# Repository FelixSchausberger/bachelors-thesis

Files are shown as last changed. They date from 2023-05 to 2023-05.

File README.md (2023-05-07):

# Design and Construction of a Delta Robot to Study Inverse Kinematics

Bachelor's thesis: University of Applied Sciences Technikum Wien, 2019
This project aims at designing a delta robot to study inverse kinematics in an educational environment.

<p align="center">
  <a href="https://github.com/FelixSchausberger/bachelors_thesis">
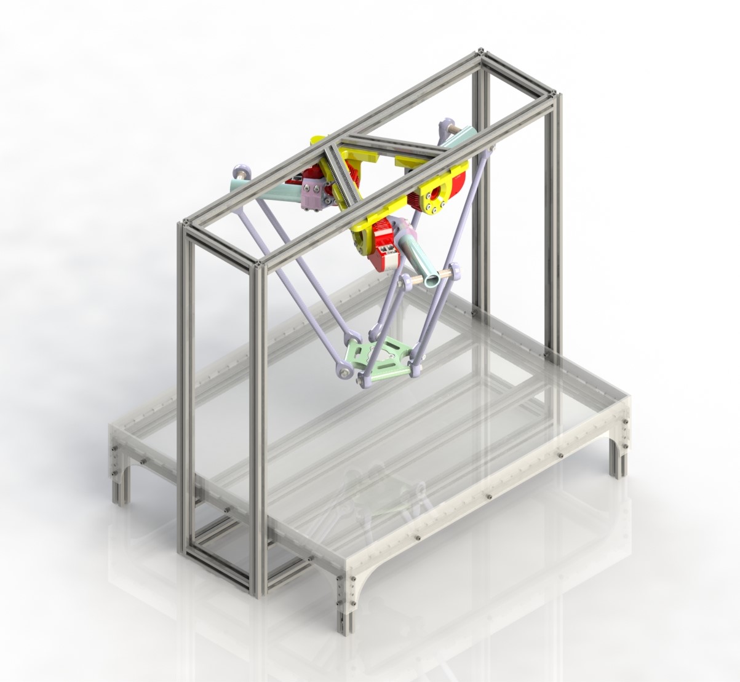
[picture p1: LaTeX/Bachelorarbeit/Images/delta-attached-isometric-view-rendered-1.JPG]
Delta Robot
    
  </a>
</p>
<br/>
<p align="center">
  <a href="https://github.com/FelixSchausberger/bachelors_thesis/blob/main/LaTeX/Bachelorarbeit/Bachelorarbeit.pdf" title="Download PDF (full text)">
    
  </a>
  <a href="https://github.com/FelixSchausberger/bachelors_thesis/blob/main/LaTeX/Paper/Paper.pdf" title="Download PDF (full text)">
    
  </a>
</p>
<br/>

## Abstract

The ever-increasing influence of automation in various branches of industry makes the acquisition of technological competencies a key element for the success of future generations of students.

However, despite efforts to reform education, much of the current teaching system continues to prepare students for the future by using methods from the past. Current educational curricula often lack opportunities to provide interdependencies between individual areas of engineering. Trainees are often unable to establish connections between them. By providing an appropriate and approachable entry point, the versatile field of designing robotic systems could be made more accessible to aspiring engineers.

As an approach, in the present thesis, the development of a prototype of a parallel kinematic machine, a Delta-robot, is presented. The system integrates knowledge from mechanics, electrical engineering and computer science. To allow a modular structure, the entity is realized via ''smart'' drives. The robot can thus be dynamically changed upon request to be customized to specific tasks. The drives facilitate the development, as the robot can be modulated quickly and inexpensively. In addition, the modular hardware in combination with open source software does neither require any specialized industrial equipment nor research establishments to impart practice-oriented content and research opportunities.

As a result, through the interaction of these advantages, a prototype for didactic purposes in academic education can be manufactured in an intrinsically safe, portable and cost-effective manner to give prospective engineers the unique opportunity of studying parallel kinematic machines in a practical way.

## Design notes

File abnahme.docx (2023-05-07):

Titel: Auslegung und Konstruktion eines Delta-Roboters zur Untersuchung der inversen Kinematik

Erklärung: Kinematik beschreibt Stellungen, Geschwindigkeiten und Beschleunigungen der Gelenke in Relation zu den Bewegungen des Endeffektors (Bewegungslehre)

- Direkte Kinematik: Definiert Pose des Endeffektors bei gegebenen Gelenkwinkel
- Inverse Kinematik: Liefert bei bekannter Pose des Endeffektors die entsprechenden Gelenkwinkel

Motivation/Aufgabenstellung

- Bereitstellung eines geeigneten Einstiegspunkts für angehende Ingenieure in ILV AURO schaffen
- Integriert anwendungsbezogen Wissen aus Mechanik, Elektrotechnik und Informatik
- Roboter für didaktische Zwecke in der akademischen Ausbildung:

Eigensicher (Sicherheit für Mensch und Maschine), portabel & kompakt (wechselnde Räumlichkeiten), robust, kostengünstig

Warum Parallelkinematik? ( & was ist überhaupt eine Parallelkinematik? → Hand, Regenschirm)

- Parallele Strukturen aufgrund der parallel ablaufenden Bewegungsvorgänge oftmals nur schwer nachvollziehbar
- Lösen der inversen Kinematik im Vergelich mit seriellen Strukturen relativ einfach -> erleichterter Einstieg

Warum smarte Motoren?

- Modulare Struktur (dynamische Konfiguration bei Anforderungsänderungen)
- Schnelle und kostengünstige Modulierung
- Benötigen kein spezielles industrielles Equipment (Nur Strom & Ethernet)

Vorgehensweise, Praktische Durchführung & Beitrag

- Geometrische Modellierung
  - Parameter orientieren sich an in der Industrie eingesetzten Robotern
- Mathematische Modellierung
  - Ermittlung der Freiheitsgrade und Berechnung der inversen Kinematik
- Konstruktion und Programmierung
  - Um Modell der inversen Kinematik am Testaufbau auf Richtigkeit zu überprüfen
  - Fertigungsverfahren: Rapid Prototyping (additiv, SLS)
  - Bei der Baugröße und den Befestigungsmöglichkeiten wurde darauf geachtet, den Roboter benutzerfreundlich, kompakt und modular zu gestalten, um Erweiterungen zu ermöglichen und Wartungsarbeiten zu erleichtern.

Ergebnisse (bis jetzt)

- Herstellung eines Prototyps für didaktische Zwecke in der akademischen Ausbildung eigensicher, transportabel und kostengünstig, um angehenden Ingenieuren die einzigartige Möglichkeit zu bieten, parallelkinematische Maschinen praxisorientiert zu studieren
- Gewünschtes Ziel erfüllt. Aufbau bestätigt Funktionsfähigkeit der Algorithmen und zeigt, dass das System wie erwartet bei bekannter Pose des Endeffektors die entsprechenden Gelenkwinkel liefert und der Steuerung zur Trajektorieplanung übergibt.

Ergebnisse (bis Abgabe)

- Verfeinerung der Trajektorieplanung
- Optimierung des GUIs
- Fertigstellung der theoretischen Arbeit

Diskussion

- Auslegung von Robotersystemen erfordert eine hohe Erfahrung von Seiten der Entwickler
- Verbesserungspotenziale für weiterführende Arbeiten
  - Regelungsstrategie (dynamische Verhalten des Roboters)
  - Positionier- und Wiederholgenauigkeit
    - Trajektorienplanung
    - Fertigungs- und Montagetoleranzen der mechanischen Struktur
  - Algorithmen
    - Zeitoptimierung
    - Optimierung der Linearisierung der Pfade
- Arbeitsraumanalysen, Singularitätsuntersuchungen, dynamischen Modellierungen des Roboters

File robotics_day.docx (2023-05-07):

Auslegung und Konstruktion eines Delta-Roboters zur Untersuchung der inversen Kinematik

Motivation/Aufgabenstellung

Auslegung und Konstruktion eines Prototyps einer parallelkinematischen Maschine

- Bereitstellung eines geeigneten und zugänglichen Einstiegspunkts als Lösungsansatz für einen erleichterten Einstieg der Konstruktion und Auslegung von Robotern
- Im Betriebszustand ist die Sicherheit für Mensch und Maschine zu gewährleisten, während aufgrund wechselnder Räumlichkeiten der Aufbau portabel gestaltet werden muss. Daraus resultieren Anforderungen einer möglichst kompakten als auch eigensicheren, robusten Konstruktion, welche dennoch möglichst kostengünstig gefertigt werden soll.

Warum Parallelkinematik (& was ist überhaupt eine Parallelkinematik?)

- Serielle Kinematik: Hand, Parallel Kinematik: Regenschirm
- Auslegung paralleler Strukturen aufgrund der Komplexität parallel ablaufender Bewegungsvorgänge oftmals nur schwer nachvollziehbar
- Die Kinematik beschreibt Stellungen, Geschwindigkeiten und Beschleunigungen der Gelenke in Relation zu den Bewegungen des Endeffektors und bildet somit die Grundlage für diverse Untersuchungen. Die Bewegungslehre kann in zwei mathematische Modellierungen, der direkten und der inversen Kinematik, unterschieden werden. Die direkte Kinematik definiert die Pose des Endeffektors bei gegebenen Gelenkwinkel, während die inverse Kinematik bei bekannter Pose des Endeffektors die entsprechenden Gelenkwinkel liefert.
- Lösen der inversen Kinematik im Vergleich mit seriellen Strukturen relativ einfach -> erleichterter Einstieg

Warum smarte Motoren?

- modulare Struktur
- dynamische Konfiguration bei Anforderungsänderungen
- schnelle und kostengünstige Modulation
- benötigen kein spezielles industrielles Equipment (Nur Strom & Ethernet)

Vorgehensweise, Praktische Durchführung & Beitrag

- Geometrische und mathematische Modellierung des Systems
  - Ermittlung der Freiheitsgrade und Berechnung der inversen Kinematik
  - Parameter orientieren sich an in der Industrie eingesetzten Robotern
- Konstruktion und Programmierung
  - Um Modell der inversen Kinematik am Testaufbau auf Richtigkeit zu überprüfen
  - Fertigungsverfahren: Rapid Prototyping (additiv, SLS)
  - Bei der Baugröße und den Befestigungsmöglichkeiten wurde darauf geachtet, den Roboter benutzerfreundlich, kompakt und modular zu gestalten, um Erweiterungen zu ermöglichen und Wartungsarbeiten zu erleichtern.

Ergebnisse (bis jetzt)

- Herstellung eines Prototyps für didaktische Zwecke in der akademischen Ausbildung eigensicher, transportabel und kostengünstig, um angehenden Ingenieuren die einzigartige Möglichkeit zu bieten, parallelkinematische Maschinen praxisorientiert zu studieren
- Gewünschtes Ziel erfüllt. Aufbau bestätigt Funktionsfähigkeit der Algorithmen und zeigt, dass das System wie erwartet bei bekannter Pose des Endeffektors die entsprechenden Gelenkwinkel liefert und der Steuerung zur Trajektorieplanung übergibt.

Ergebnisse (bis Abgabe)

- Verfeinerung der Trajektorieplanung
- Optimierung des GUIs
- Fertigstellung der theoretischen Arbeit

Diskussion

- Die Auslegung und Entwicklung von Robotersystemen erfordert eine hohe Erfahrung von Seiten der Entwickler, auch wenn das gewünschte Ziel erreicht wurde, gibt es dennoch umfangreiche Verbesserungspotenziale.
- In weiterführenden Arbeiten kann die verwendete Regelungsstrategie optimiert werden, um das dynamische Verhalten des Roboters zu verbessern. Um die Positionier- und Wiederholgenauigkeit zu verfeinern kann zudem eine angemessene Trajektorienplanung ausgelegt werden. Diesbezüglich können auch die Algorithmen verbessert werden, indem diese zum Beispiel zeitoptimiert werden. Darüber hinaus kann die Linearisierung der Pfade optimiert werden. Bei der Positionier- und Wiederholgenauigkeit spielen auch die Fertigungs- und Montagetoleranzen der mechanischen Struktur eine entscheidene Rolle. Abschließend können sich zukünftige Arbeiten mit Arbeitsraumanalysen, Singularitätsuntersuchungen sowie dynamischen Modellierungen des Roboters befassen.

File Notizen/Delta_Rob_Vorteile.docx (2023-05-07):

Vorteile Parallelroboter:

Parallelroboter eignen sich aufgrund der Vorteile parallel kinematischer Mechanismen, wie etwa dem hohen Last-Gewichts-Verhältnis und der hohen dynamischen Leistung besser für die Durchführung von Bearbeitungsvorgängen als serielle Mechanismen [6, 7].

\cite{Cr17}

Parallelkinematiken weisen im Vergleich zu seriellen Kinematiken eine ganze Reihe von Vorteilen auf. Besonders hervorzuheben sind die geringen zu bewegenden Massen sowie die günstigen dynamischen Eigenschaften. Bei entsprechender Wahl der Gelenke werden die Glieder überwiegend auf Druck oder Zug beansprucht. Im Vergleich zu Industrierobotern ist besonders die hohe Wiederholgenauigkeit hervorzuheben. Natürlich gibt es auch Nachteile, so z. B. der im Verhältnis zum Bauraum relativ kleine Arbeitsraum, die teilweise geringen Schwenkwinkel und die durch Koordinatentransformation aufwändige Steuerung.

\cite{Ne06}

Parallelroboter haben gegenüber Serienrobotern viele Vorteile. Die Hauptvorteile sind die Stabilität der Mehrfachlenker und die Geschwindigkeit aufgrund der geringen Trägheit. Parallele Manipulatoren weisen jedoch einige Nachteile auf, zum Beispiel, dass sie im Vergleich zu einem seriellen Roboter ähnlicher Größe ein eingeschränktes Arbeitsraumvolumen aufweisen. Es gibt viele beschriebene Parallelroboter, von denen der erste Gough [1] und Stewart [2] zugeschrieben wird. Es gibt viele mögliche Variationen von Parallelrobotern [3], die jeweils Vor- und Nachteile haben. Ein Parallelroboter, der kommerziellen Erfolg hatte, ist der Delta-Roboter [4, 5, 6] (siehe Abb. 1). Der Delta-Roboter hat sich in der Industrie als gute Bestückungsmaschine für relativ leichte Lasten etabliert.

\cite{Ho12}

Aufgrund ihrer kinematischen Konfiguration mit offenem Regelkreis und Cantilever-Typ verfügen serielle Roboter über große Arbeitsbereiche und hohe Fingerfertigkeit, leiden jedoch unter mangelnder Steifigkeit und relativ großen Positionierungsfehlern. Da jeder unabhängige Schenkel eine geschlossene Schleife bildet und Basis und bewegliche Plattform verbindet, können parallele Roboter eine hohe Steifigkeit und ein hohes Kraft-Gewichts-Verhältnis erreichen. Parallele Roboter sind jedoch für einen eingeschränkten Arbeitsbereich und geringe Fingerfertigkeit bekannt. Das heißt, Serienroboter und Parallelroboter haben ihre eigenen Vor- und Nachteile.

Seit der Erfindung von Clavel in den 1980er Jahren [14] wurde der Delta-Parallelmechanismus dank seiner herausragenden Eigenschaften wie Lichtstruktur, Schnelligkeit, Hochpräzision und Schnelligkeit in vielen Bereichen [15] erfolgreich eingesetzt einfach zu steuern. Untersuchungen zum Delta-Parallelmechanismus umfassen fast alle Aspekte [16-18].

\Li{14}

The core advantage of delta robots is speed. When typical robot arm has to move not only payload, but also all servos in each joint, the only moving part of delta robot is its frame, which is usually made of lightweight composite materials. To get an evidence of delta robots outstanding abilities, take a look at this and this video. Due to its speed, delta robots are widely used in pick-n-place operations of relatively light objects (up to 1 kg).

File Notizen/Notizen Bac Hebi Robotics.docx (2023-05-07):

Notizen Bac Hebi Robotics 14.02.2018

Bestehende modulare Roboterantriebe/-aktoren:

Kommerziell erwerbbar:

- HEBI X5 und X8 von CMU (CMU: Biorobotics lab at Carnegie Mellon University)
  - X5: 20W Spitzenausgangsleistung

Bemerkenswert: Software und API zur Steuerung dieser Aktuatoren - gut dokumentiert, einfach zu bedienen und reich an Funktionen.

\cite{Ka18}

X-Module: Standardschrauben
Passiver Schnittstellen: zur Übertragung von elektrischer Energie, zur Kommunikation und um Struktur zu schaffen. Ermöglichen auch Anschluss externer Geräte wie Kameras, Lidar oder Endeffektoren zur Manipulation.

Verbindungen zwischen Modulen: Standard Ethernet-Kabel mit Standard Kommunikationsprotokollen

Jedes Hardwaremodul wird zusätzlich zur Ansteuerung mit einem Beschleunigungssensor, Gyroskop, Winkelcodierer und Mikrocontroller für die Steuerungsverarbeitung auf niedriger Ebene geliefert.

Unsere neueste Hardware verwendet auch die serienelastische Betätigung (SEA) [6], bei der die Stellantriebe mechanische Federn am Ausgang ihrer Antriebsstränge enthalten.

Die Integration der Serienelastizität in Roboter kann die Probleme herkömmlicher Roboteraktuatoren abmildern, wodurch eine genaue Erfassung des Ausgangsdrehmoments ermöglicht wird und Aufprallkräfte aufgenommen werden, die die Antriebsmechanismen beschädigen könnten [6].

\cite{AnWh17}

Im Handel erhältlich 6 Grad Roboterarmsysteme (DOF) wie KUKA [1], Universalroboter [2] usw. sorgen für eine Vielzahl von Manipulationen Aufgaben. Diese Roboterarme können jedoch nicht für spezielle Aufgaben modifiziert werden, noch können sie neu konfiguriert werden, wenn sich Anforderungen ändern. Stattdessen konstruierte Roboterarme mit rekonfigurierbaren, modularen Teilen können individuell angepasst werden. Daher haben zB HEBI-Robotik [3], Modbot [4] begonnen, neuere kommerzielle Robotersysteme mit anpassbarem Design durch modulare Bauweise zu fördern.

\cite{DeSa18}

Robotik und Automatisierung haben heute einen großen Teil der Fertigungsindustrie revolutioniert. Roboter sind in der Lage, viele Aufgaben effizienter und konsistenter zu erledigen als ein Mensch.

\cite{FrDe18}

Andere Elemente, die für den Fortschritt von Robotern von entscheidender Bedeutung waren, sind die mit großen Funktionen verbundenen Fähigkeiten Daten, Cloud Computing, 3D-Herstellung und die Entwicklung von Open-Source-Hardware Erleichterung des Roboterbaus.

„Aufgrund der zunehmenden Verbreitung von Open-Source-Software und modularer Hardware müssen Sie nicht eine spezialisierte industrielle Einrichtung oder ein universitäres Forschungslabor, um mit dem Bau von Robotern zu beginnen “, sagte Vikram Kapila, Professor für Maschinenbau und Luft- und Raumfahrttechnik an der New York University Tandon School of Engineering. „Menschen können tatsächlich an Robotik basteln, ohne die Bank zu brechen und ohne immer und immer wieder die gleichen Lösungen zu finden. Sie können jetzt verwenden standardisierte Roboterbau-Lösungen. “

Zu den Open-Source-Systemen oder Gebäudemodulen für die Robotik-Entwicklung gehören die Robotik Betriebssystem oder ROS, das von der Open Source Robotics Foundation und HEBI Robotics überwacht wird, eine Firma, die von Robotikexperten der Carnegie Mellon University gegründet wurde Bausteine, die als „Aktuatoren“ bezeichnet werden und die so konfiguriert werden können, dass sie benutzerdefinierte Roboter bauen, die es sein können gesteuert von einem Smartphone oder Tablet-Computer.

\cite{He18}

Modulare Robotersysteme können mit einer einzigen Plattform an unterschiedliche Aufgaben angepasst werden und ermöglichen die Entwicklung von anpassbaren Robotern, die schneller und kostengünstiger als herkömmliche Roboter entwickelt werden können. Eine Herausforderung bei der Verwendung solcher Roboter ist das Bestimmen des optimalen Designs, um einen Roboter für eine bestimmte Aufgabe zu spezialisieren. Ein optimaler kundenspezifischer modularer Manipulator wäre effektiver und erfordert weniger redundante Komponenten als ein generischer Manipulator. Man könnte seine Baugruppe leicht neu konfigurieren, um auf eine Änderung der Aufgabe zu reagieren, was ein schnelles Redesign und Prototyping unterstützt.

\cite{WhCh18}

Eine Weiterentwicklung der SEA-Module ist die neu entwickelte X5-Serie, die in Kapitel 2.5.3 beschrieben wird. Sie wurden entwickelt, um abhängig von der Anwendungsdomäne modulare Robotermanipulatoren zu erstellen.

Die in Abbildung 10 gezeigte X5-Serie richtet sich an Forscher, Ingenieure und industrielle Integratoren. Sein modulares und leichtes Design ermöglicht die schnelle Erstellung benutzerdefinierter Roboterkonfigurationen. Wie die SEA-Module sind sie mit kostengünstigen, aber zuverlässigen Inertial Measurement Units (IMU) ausgestattet. Die Eingabebefehle ermöglichen auch die Steuerung von Position, Geschwindigkeit und Drehmoment. Der serienelastische Aktuator wird von einem bürstenlosen Motor angetrieben, der im Gegensatz zum eingeschränkten Bewegungsbereich der SEA-Module eine kontinuierliche Ausgangsdrehung ermöglicht. Zur Steuerung der Aktuatoren werden APIs für MATLAB, ROS und C / C ++ unterstützt. Weitere Details finden Sie in [15].

Die Ausrichtung des Beschleunigungsmessers und des Gyroskops ist in Abbildung 11 dargestellt. Die x- und y-Achse sind durch die Pfeile angegeben. Die Z-Achse zeigt direkt aus dem Bild. Für die Verbindungslängenschätzung muss der Standort der IMU im Modul bekannt sein. Das blaue Quadrat zeigt die Position der Sensoren an.

Wie in Kapitel 2.5.3 beschrieben, können die HEBI-Stellantriebe durch Eingabe von Stellungs-, Geschwindigkeits- und Drehmomentbefehlen gesteuert werden. PID-Regelkreise werden verwendet, um diese drei Eingänge zu kombinieren. Die Steuermodi verwenden unterschiedliche Regelkreissequenzen, abhängig davon, welches Eingangssignal bevorzugt werden soll. Jeder PID-Regler für jedes Eingangssignal (Position, Geschwindigkeit, Drehmoment) hat seine eigenen PID-Parameter. Das bedeutet, dass der Proportional-, Integral- und Differentialanteil für jeden der drei Regler abgestimmt werden muss. Derzeit gibt es zwei prominente Steuerungsmodi: Control Mode Strategy (CMS) 3 für die Lageregelung und Control Mode Strategy 4 für die Drehmomentregelung [16]. Das CMS 3 hat keine äußere Drehmomentschleife und wird zur Lageregelung verwendet. Wie in Abbildung 12 dargestellt, werden Position, Geschwindigkeit und Drehmoment PID summiert, um das Motorsignal zu erzeugen.

Zur Drehmomentsteuerung wird dieser Modus verwendet. Ein Vorwärtsdrehmomentsignal wird mit der Position PID-Ausgabe summiert, um ein Drehmomentsignal zu erzeugen, und wird dann an den PID-Regler für das innere Drehmoment übergeben. Dieser Ausgang wird dann mit dem Geschwindigkeits-PID-Signal summiert, um die Motor-PWM-Befehle zu erzeugen, wie in 13 gezeigt.

Die Verwendung von externen Messsystemen wie Kameras ist nicht immer anwendbar. In einigen Umgebungen ist möglicherweise keine korrekte Kameraeinstellung möglich. Außerdem muss ein solches System kalibriert werden und fügt einen weiteren Fehler- und Fehlerpunkt hinzu. Wenn möglich, sollten daher nur propriozeptive Sensoren verwendet werden. Wie in Kapitel 2.5.3 erwähnt, sind die Sensoren in den X5-Modulen kostengünstig. Im Vergleich zu teuren Sensoren, bei denen es sich möglicherweise sogar nicht um Einzelchip-Bausteine handelt, wie bei den in den SEA- und X5-Modulen verwendeten IMUs, sind ein gewisses Eigenrauschen, Drift und eine geringere Genauigkeit zu erwarten. Folglich muss ein entsprechendes Verfahren dies berücksichtigen.

Ansätze, bei denen eine IMU am Endeffektor des Manipulators eingesetzt wurde, zeigten vielversprechende Ergebnisse, wie in [26] gezeigt. Der Vorteil der SEA- und X5-Module besteht darin, dass jedes Modul, nicht nur der Endeffektor, eine eigene IMU enthält. Dementsprechend ist ein Ansatz, der den Multisensor-Setup nutzt, wünschenswert und könnte die Genauigkeit verbessern.

\cite{Wi16}

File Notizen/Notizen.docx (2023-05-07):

Keine Gegenüberstellungen, kein Projekt Bericht! Konkretisierung kommt von uns!!

SdT: 1-2 Seiten, 5-10 Quellen: Welche Delta Roboter gibt es? Wie ist ein Delta Roboter aufgebaut? Realisieren andere Firmen ähnliche Projekte mit diesen Motoren/dieser Problemstellung?

KONKRETISIEREN!!! (Passt auf A4/A3 Blatt, ..)

Realisierung eines Delta Roboters für die Forschung und Lehre

-> Deltakinematik

Keywords:

Smart Motoren, Smarte Antriebe (moderne), Industrierobotik, Robotics in education, educational robotics

Was ist smart? (Hebi Motoren: >49 Sensoren, welche Schnittstellen, ..)

Überlegungen:

Möglichst Kompakt (wird in EDV Saal verwendet)

Roboter als "Black Box" vermeiden - möglichst ersichtlich/anschaulich gestalten

Lernmethoden und Übungen nicht wie Rezept gestalten - in eine Anwendung/Geschichte verpacken

Tischbeine:

-300: 206.29

-350: 157.13 - 4 = 153.13

-375: 132.09 - 4 = 128.09 -> 128 [mm] ( ! ) -> 120 [mm]

-400: 107

BAC:

Deltakinematik: 3D Printer: Marlin

Projektziele:

Realisierung einer Clavel's DELTA-Roboters.

Vollständiger Beschreibung der inversen Kinematik der geschlossenen kinematischen Kette.

Implementierung einer Applikation (Pick-and-Place Aufgabe, Malen in einem Sandbecken).

Modularer Aufbau, alle Verbindungen werden gesteckt oder geschraubt.

Einhausung des Roboters mit 20 $[mm]$ Aluprofilrahmen.

Die aktiven Gelenke des Roboters werden mit HEBI X5-1 Motoren realisiert.

Die passiven Gelenke des Roboters werden mit Doppelgelenklager realisiert.

Kurzfassung:

Den Themenkreis und die behandelte Problematik, um die Motivation der Arbeit zu erklären („Worum geht es und warum?“).

Den eigenen Beitrag der Arbeit (Kernaussage, These, engl. „thesis“) hinsichtlich Neuheitswert (Originalität) und Relevanz („Mein Ergebnis – und warum es neu und wichtig ist“).

Den Nachweis der Überprüfbarkeit (Thesenprüfung, engl. „Proof of concept“), unter anderem die Methode und die Skizze der Beweisführung (formal, argumentativ oder empirisch) und wesentliche quantitative oder qualitative Ergebnisse und Erkenntnisse der Arbeit („Warum soll der/die LeserIn meinem Ergebnis vertrauen?“).

Bac Arbeit:

search strings:

((teaching OR learning OR teach OR learn OR education OR educational)

AND

(robotic OR robotics OR robot OR robots))

((smart OR intelligent)

AND

(engine OR motor OR drive))

IOT smart manufacturing

Rolls-Royce: IntelligentEngine

(smart AND IOT AND IIOT AND big data AND (robotic OR robotics OR robot OR robots))

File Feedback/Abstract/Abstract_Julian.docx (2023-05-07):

Abstract – Julian Katzenschwanz – Mr16b034

Image recognition and robot control are often used together in automation - for example, when chocolates are packaged with the help of a camera system and a delta robot. In education, however, image recognition is often done only virtually, without solving practical problems. An educational demonstrator has to be provided to reinforce through practical exercises what has been learned virtually before. It has to be compact and reliable to be justifiable as a suitable learning tool for academic faculties. Likewise, a high utilization should be sought to increase the systems relevancy. This work uses an online demonstrator to reach more users. A cartesian robot in gantry design is built and equipped with a camera and a magnet as the end effector. The robot is controlled online via widely used G-code. The system is thus able to internationally deliver footage of the puzzle for image recognition via the camera. After localizing the puzzle pieces in an image recognition exercise, the robot can be used to test the applied methods as a practical example to solve puzzles. The robot is capable of its designed task, but the whole process still has to be improved to function as an operational demonstrator. Future work could be done on improvements to the camera system, development of different puzzles, writing an instruction manual and educational exercises.

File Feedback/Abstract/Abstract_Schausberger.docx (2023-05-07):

The ever-increasing influence of industrial sectors makes the acquisition of technological competences a key element for the success of the next generation of students. However, despite efforts to reform education, much of the current teaching system continues to prepare students for the future, using methods from the past. Current educational curricula often lack opportunities to provide interdependencies between individual areas of engineering. Trainees are often unable to establish connections between them. By providing an appropriate and approachable entry point the versatile field could be made more accessible to aspiring engineers. In this thesis, the mechatronic design of a robotic system as an approach to reinforce educational access to constructing and designing robots is presented. For this purpose, a prototype of a parallel kinematic machine, a DELTA robot, is being developed. The system integrates knowledge from mechanics, electrical engineering and computer science. To allow a modular structure, the entity is realized via ''smart'' drives. The robot can thus be dynamically changed upon request to be customized to specific tasks. The drives facilitate the development, as the robot can be modulated quickly and inexpensively. In addition, the modular hardware in combination with open source software does not require any specialized industrial equipment or research establishments to impart practice-oriented content and research opportunities. As a result, through the interaction of these advantages, a prototype can be manufactured in an intrinsically safe, portable and cost-effective manner to give prospective engineers the unique opportunity of studying parallel kinematic machines in a practical way.

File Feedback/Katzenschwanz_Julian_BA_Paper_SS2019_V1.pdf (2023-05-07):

Bachelor-Studiengang Mechatronik/Robotik
FH Technikum Wien, Höchstädtplatz 6, A-1200 Wien

ONLINE GESTEUERTE LEHRPLATTFORM FÜR BILDERKENNUNG UND ROBOTERSTEUERUNG

StudentIn: KATZENSCHWANZ, Julian PK: 1610330034 FH-BetreuerIn: SCHREMSER, Dominik, BSc

Kurzfassung: Bilderkennung und Roboterkontrolle werden in
der | Automatisierung | häufig | gemeinsam | eingesetzt | -
beispielsweise beim Verpacken von Pralinen mit Hilfe eines Kamerasystems und eines Delta-Roboters. In der Ausbildung erfolgt die Bilderkennung jedoch oft nur virtuell, ohne praktische Probleme zu lösen. Es sollte ein Demonstrator bereitgestellt werden, um durch praktische Übungen das virtuell Gelernte zu vertiefen. Dieser muss kompakt und zuverlässig sein, um ihn als geeignetes Lerninstrument für akademische Fakultäten rechtfertigen zu können. Ebenso sollte eine hohe Auslastung angestrebt werden, damit die Anlage durchgehen relevant ist. Diese Arbeit bildet die Grundlage für einen Online-Demonstrator, um mehr Nutzer zu erreichen. Ein kartesischer Roboter in Portalbauweise wird entwickelt und mit einer Kamera und einem Elektromagneten als Endeffektor ausgerüstet. Der Roboter wird online über eine numerische Steuerung betrieben. Nach der Lokalisierung der Puzzleteile in einer Bilderkennungsübung kann der Roboter zum Testen der angewendeten Methoden und als praktisches Beispiel zum Lösen der Puzzles verwendet werden. Der konstruierte
Portalroboter | ist | in | der | Lage, | Puzzleteile | mithilfe
standardisierter | numerischer | Steuerungssprachen | zu
manipulieren. Ein Konzept für die Online-Implementierung der Kamera und der Steuerungsschnittstelle wurde entwickelt, aber im Rahmen dieser Arbeit nicht umgesetzt. Der Portalroboter ist in der Lage seine vorgesehene Aufgabe zu erfüllen, der Gesamtprozess muss aber noch verbessert werden, um eine funktionelle Lehrplattform zu erhalten. Zukünftig könnte an der
Implementierung | des | Kamerasystems | und | der
Onlineverbindung, der Entwicklung unterschiedlicher Puzzle und dem Erstellen von Bedienungs- und Übungsanleitungen gearbeitet werden.
Schlüsselwörter: Bilderkennung, Robotersteuerung, G-Code,
Online | Lehrplattform, | Demonstrator, | ferngesteuerte
Laboratorien.

### 1. EINLEITUNG

Bilderkennung | und | Roboterkontrolle | sind | zwei
Problemstellungen, | die | häufig | gemeinsam | in | der
Automatisierungstechnik auftreten – zum Beispiel um Bauteile auf einem Förderband zu erkennen und per Pick-and-Place-Anwendung korrekt einzusortieren.
In der Lehre wird Bilderkennung oft nur virtuell abgehandelt, ohne Bezug zu praxisnahen Problemstellungen
[1]. | Für | Roboterkontrolle | wird | dagegen | meist | auf
Simulationssoftware | zurückgegriffen | oder | auf | simple
Einführungsübungen an teuren Industrierobotern, falls diese im Lehrinstitut überhaupt vorhanden sind.
Ein | vereinen dieser | zwei | Lehrbereiche in | einer
praktischen, praxisnahen Übung würde helfen gelerntes zu verfestigen, ein reales Gefühl für Industrieanwendungen schaffen und Interesse an Automatisierungstechnik wecken [2]. Dazu wird ein Demonstrator benötigt, anhand dessen Übungen vollzogen werden können.

### 2. PROBLEM- UND AUFGABENSTELLUNG

Ziel dieser Bachelorarbeit ist das Entwickeln und Fertigen eines Demonstrators für die Lehre. Dieser soll Online steuerbar sein, um Studenten überall auf der Welt zur Verfügung zu stehen. Das Hauptaugenmerk der Lehrapplikation ist die praktische Umsetzung von Bilderkennungsmethoden an einem Roboter.
Der Fokus der Arbeit liegt somit im Entwickeln und Fertigen einer soliden Roboterplattform, die als Grundlage des Demonstrators dienen soll. Nach robuster Erfüllung dieser Ziele wird die Vervollständigung der Lehrplattform angestrebt, besonders die Kamera- und Onlineimplementierung, da diese wesentliche Bestandteile der Lehrplattform sind.

### 3. MATERIALIEN UND METHODEN

Die Entwicklungsarbeit hält sich an das Drei-Ebenen-Vorgehensmodell nach Bender. Dabei werden besonders auf
die | Unterteilung | in | System-, | Subsystem- | und
Komponentenebene, als auch auf den Mechanik-, Hardwareund Softwarestränge wertgelegt [3]. Kombiniert wird das
Vorgehensmodell | mit | einer | Vereinfachung | des | agilen
Rahmenwerks von Scrum, was die angewendete Organisationsund Kommunikationsart maßgeblich formt [4]. Dies wird mithilfe des Projektmanagementtools Trello umgesetzt und in Form von Karten und Checklisten festgehalten.

### 4. PRAKTISCHE DURCHFÜHRUNG

Für die Entwicklung und Fertigung des Portalroboters wurde ein vollständiges, maßgetreues CAD-Modell (Computer-Aided Design) erstellt. Dies beinhaltet die Positionen und Maße aller relevanten Bauteile des echten Roboters.

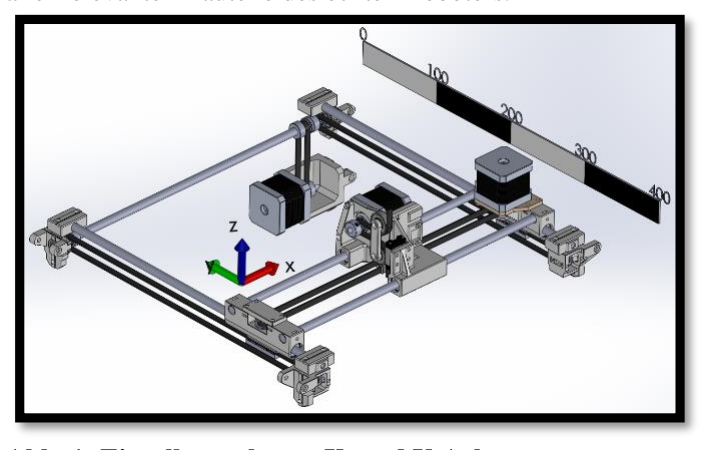
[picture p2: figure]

Abb. 1: Einzelbetrachtung X- und Y-Achse

Die Abb. 1 zeigt den Aufbau der X- und Y-Achsen. Die zwei Rundführungen der Y-Achse sind am Rahmen aufgehängt. Beide haben je einen angetriebenen Schlitten, auf dem die zwei
Rundführungen, | Umlenkrolle | und | der | Motor | mit
Zahnriemenscheibe der X-Achse befestigt sind. Die Bewegung der beiden Y-Schlitten wird über eine Welle synchronisiert, welche von einem der Schrittmotoren angetrieben wird.

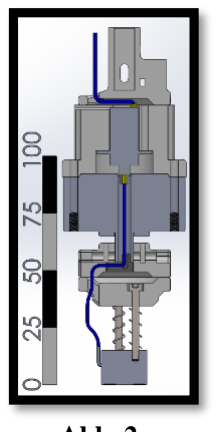
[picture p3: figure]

Ein weiterer Schrittmotor bewegt die Profilschiene der Z-Achse, in dem er einen Zahnriemen antreibt, der über zwei Kugellager umgelenkt wird. Der Motor sowie der Schlitten der Profilschiene sind dabei am Schlitten der X-Achse montiert. Der Endeffektor (Abb. 2) besteht
aus | einem | Elektromagneten, | einer
Federung mit 5,5mm Federweg, einem
Hohlwellenschrittmotor | und | einem
Schleifring. Der Verlauf der Kabel des Elektromagnets ist in Blau dargestellt. Der Schleifring erlaubt kontinuierliche Rotation des Elektromagneten, da somit keine Kabel verdreht werden.

### 5. ERGEBNISSE UND DISKUSSION

Der in Abb. 3 zu sehende Portalroboter ist das Ergebnis dieser Arbeit. Er ist imstande über das Anfahren von drei Endschalter einen Homing-Zyklus durchzuführen, bei dem er seine X-, Y- und Z-Koordinaten Nullsetzen kann. Die rotatorische A-Achse des Endeffektors kann kontinuierlich gedreht werden und benötigt dadurch keine Limitierung. Die maximalen Verfahrwege von X=215mm, Y=225mm und Z=200mm werden Softwareseitig überwacht.

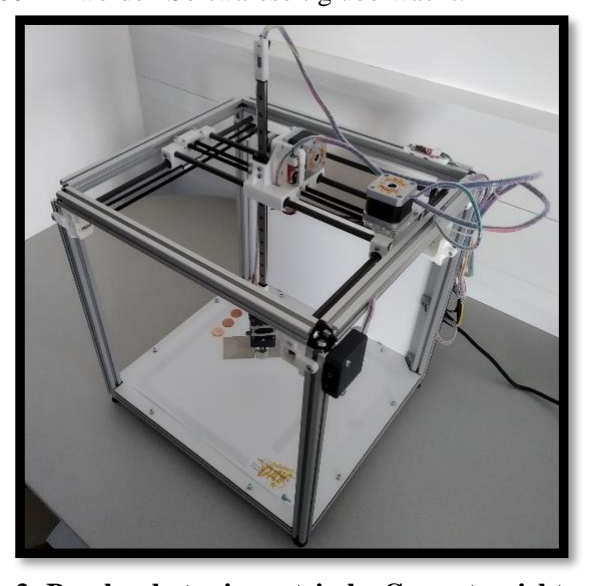
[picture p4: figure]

Abb. 3: Puzzleroboter isometrische Gesamtansicht

Der Endeffektor verfügt über einen Federweg von 5,5mm, was zusätzliche Sicherheit und Flexibilität in der Z-Achse sicherstellt. Damit können Anwenderfehler in der Wahl der Z-Koordinaten, wie z. B. nichtbeachten der Puzzleteilstärke oder
mehrere | übereinanderliegende | Puzzleteile, | ausgeglichen
werden.
Die Endeffektorhalterung, wahlweise mit oder ohne Rotationsachse, ist modular aufgebaut. Die verwendeten Flanschmaße entsprechen den von NEMA 17 Schrittmotoren, mit einem Lochabstand von je 31mm für M3 Schrauben. Der Schleifring bietet eine Kabeldurchführung von 12 Polen. Dies ermöglicht Flexibilität beim Wechseln der Endeffektoren, sollten zukünftige Änderungen dies verlangen.
Der Roboter verfügt über einen Kippschalter, der die 12V Generation des Netzgeräts steuert. Dadurch können die Aktuatoren des Roboters einfach stromlos geschalten werden, um beispielsweise den Roboter händisch zu bewegen, ohne die Steuerung ebenso deaktivieren zu müssen.
Der Endeffektor weist ein hohes Spiel in Nähe der Puzzlefläche auf, verstärkt durch die Länge der ausgelenkten Z-Achse. Dies ist hauptsächlich bedingt durch ein Spiel zwischen den Gleitlagern und dem Schlitten der X-Achse – aber auch durch die Flexibilität der verwendeten Polyamid SLS-Strukturbauteile, sowie die der Aluminium-Rundführungen. Während das Spiel mit ±2mm in X-Richtung und ±4mm in
Y-Richtung | beträchtlich | ist, | fällt | es | im | praktischen

Puzzlebetrieb nur wenig ins Gewicht. Der Großteil dieses Spiels tritt nur auf, wenn der gesamte X-Schlitten angehoben wird. Im Puzzlebetrieb treten solche Querkräfte bei dem Aufnehmen und Ablegen der Puzzleteile in der Regel nicht auf, da in solchen Pick and Place Anwendungen zu diesen Zeitpunkten keine Beschleunigungen in X-Y-Ebene stattfinden dürfen, lediglich in Z-Richtung.
Unter Beachtung der Regel, dass genaues Aufnehmen und Ablegen nur unter Verwendung der Z-Achse auszuführen sind, ist eine Wiederholgenauigkeit <1mm zu erreichen.
Der Roboter wurde mit Maximalgeschwindigkeiten von 250mm/s und Beschleunigungen von 800mm/s² betrieben, was gute Ergebnisse erzielte.
Für die Ansteuerung des Roboters kann im Netzwerk über den Online G-Code Sender ChiliPeppr eine Verbindung mit einem Raspberry Pi aufgebaut werden, wodurch drahtloses Konfigurieren und Steuern des Roboters mittels G-Code Programmen und Befehlen möglich wird. Dies ist ideal zum Testen und Vorführen des Roboters, erlaubt in dieser Konfiguration aber keinen Zugriff von Computern außerhalb des Netzwerks.

### 6. ZUSAMMENFASSUNG UND AUSBLICK

In dieser Arbeit wurde ein Demonstrator konzipiert und entwickelt, der in fertiger Ausführung als Online Lehrplattform dienen soll, um Nutzern eine praktische Anwendung von
Bilderkennung | und | Roboterkontrolle | zu | bieten. | Die
systematische Vorgehensweise trug maßgeblich zum Erfolg dieser Arbeit bei.
Alle notwendigen Subsysteme wurden analysiert und
konzeptioniert, | unter | Beachtung | der | gegebenen
Rahmenbedingungen. | Anschließend | wurde | auf
Komponentenebene | der | Puzzlebot | näher | ausgearbeitet.
Vorhandene | Komponenten | wurden | evaluiert, | fehlende
Fertigteile bestellt und restliche Bauteile in CAD konstruiert und gefertigt. Das Ergebnis ist ein fertiger Portalroboter mit kontinuierlich rotierbarem Elektromagnet als Endeffektor, zur
Manipulation | von | ferromagnetischen | Puzzleteilen. | Die
Ansteuerung erfolgt nach Industriestandard über G-Code, einer numerischen Programmsprache für CNC-Maschinen.
Während diese Arbeit einen soliden Grundstein für eine einsatzfähige online Lehrplattform legt, fehlt Softwareseitig die Implementierung der Kamera und einer nutzbaren, sicheren Onlineanbindung. Im Falle der Kamera kann ein Raspberry Pi dazu genützt werden diese per MJPEG Stream online zu stellen. Die Onlineanbindung kann über einen OPC-UA Server (Open Platform Communications, Unified Architecture) am Raspberry Pi vorgenommen werden. Dabei können Daten, z. B. X-, Yund Z Koordinaten in G-Code umgewandelt und an die serielle Schnittstelle des G-Code Interpreters weitergeleitet werden. Eine konstruktive Änderung an den Schlitten der X- und Y-Achsen ist ratsam, um das Spiel zwischen Schlitten und den Gleitlagern zu eliminieren.
Für die Fertigstellung der Lehrplattform könnte weiters auch an zusätzlichen Puzzles, sowie dem Erstellen einer Bedienungs- und Übungsanleitung gearbeitet werden.

### 7. LITERATURVERZEICHNIS

[1] S. Jorda, „Viel Forschung, wenig Praxis“, Phys. J., Bd. 13, Nr. 5, S. 8, 2014.
[2] T. Roth, R. Kirsch, C. Greß, A. Schwingel, U. Hein, und J. Appel, „Authentische Anwendungsbeispiele für eine praxisorientierte Lehre in MINT-Fächern“, 2014.
[3] K. Bender, Embedded Systems - qualitätsorientierte
Entwicklung. | Berlin/Heidelberg: | Springer-Verlag
Berlin Heidelberg, 2005.
[4] K. Schwaber und J. Sutherland, „The Scrum Guide: The Definitive The Rules of the Game“, Scrum.Org and ScrumInc, Nr. November, S. 19, 2017.

Abb. 2:
Endeffektor

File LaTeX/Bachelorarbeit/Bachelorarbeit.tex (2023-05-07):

%
% FH Technikum Wien
% !TEX encoding = UTF-8 Unicode
%

\documentclass[Bachelor, BMR, ngerman]{twbook}
\usepackage[utf8]{inputenc}
\usepackage[T1]{fontenc}

% --------------------------------------------------
% CITE
% --------------------------------------------------
\newcommand{\FHTWCitationType}{HARVARD} 
\ifthenelse{\equal{\FHTWCitationType}{HARVARD}}{\usepackage{harvard}}{\usepackage{bibgerm}}

% --------------------------------------------------
% FORMAT CODE LISTINGS
% --------------------------------------------------
\usepackage[final]{listings}
\lstset{captionpos=b, numberbychapter=false,caption=\lstname,frame=single, numbers=left, stepnumber=1, numbersep=2pt, xleftmargin=15pt, framexleftmargin=15pt, numberstyle=\tiny, tabsize=3, columns=fixed, basicstyle={\fontfamily{pcr}\selectfont\footnotesize}, keywordstyle=\bfseries, commentstyle={\color[gray]{0.33}\itshape}, stringstyle=\color[gray]{0.25}, breaklines, breakatwhitespace, breakautoindent}
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
    %
    % Zusammenfassung und Ergebnisse
    Die Ergebnisse zeigen, dass durch das Zusammenspiel dieser Vorteile ein Prototyp für didaktische Zwecke in der akademischen Ausbildung eigensicher, transportabel und kostengünstig hergestellt werden kann, um angehenden Ingenieuren die einzigartige Möglichkeit zu bieten, parallelkinematische Maschinen praxisorientiert zu studieren.

}
    
\schlagworte{

    Delta-Roboter, Parallelroboter, Modellierung von Robotern, Rekonfigurierbarer Roboter

}

\outline{

    % Motivation
    % The ever-increasing influence of industrial sectors makes the acquisition of technological competences a key element for the success of the next generations of students. 
    The ever-increasing influence of automation in various branches of industry makes the acquisition of technological competencies a key element for the success of future generations of students.
    %
    % Problem statement
    However, despite efforts to reform education, much of the current teaching system continues to prepare students for the future by using methods from the past. Current educational curricula often lack opportunities to provide interdependencies between individual areas of engineering. Trainees are often unable to establish connections between them. By providing an appropriate and approachable entry point, the versatile field of designing robotic systems could be made more accessible to aspiring engineers.
    %
    % Approach
    As an approach, in the present thesis, the development of a prototype of a parallel kinematic machine, a Delta-robot, is presented. The system integrates knowledge from mechanics, electrical engineering and computer science. To allow a modular structure, the entity is realized via ''smart'' drives. The robot can thus be dynamically changed upon request to be customized to specific tasks. The drives facilitate the development, as the robot can be modulated quickly and inexpensively. In addition, the modular hardware in combination with open source software does neither require any specialized industrial equipment nor research establishments to impart practice-oriented content and research opportunities. 
    %
    % Conclusion an results
    As a result, through the interaction of these advantages, a prototype for didactic purposes in academic education can be manufactured in an intrinsically safe, portable and cost-effective manner to give prospective engineers the unique opportunity of studying parallel kinematic machines in a practical way.

}

\keywords{

    Delta-Robot, Parallel robot, Robotic modeling, Reconfigurable robot

}

\acknowledgements{

    An dieser Stelle möchte ich mich bei allen bedanken, die mich während des Studiums begleitet und unterstützt haben. Mein Dank gilt besonders der Firma HEBI Robotics und meinem Betreuer, welcher mir bei allen Fragen und Problemen mit guten Lösungsansätzen und Methoden weiterhelfen konnte. Ebenfalls möchte ich mich beim Werkstattleiter sowie den Zuständigen des generativen Fertigungslabors und dem Institut, für die Möglichkeit die Bachelorarbeit realisieren zu können, bedanken.
    
}

%%%%%%%%%%%%%%%%%%%%%%%%%%%%%%%%%%%%%%%%%%%%%%%%%%%%
%%                 BEGIN DOCUMENT                 %%
%%%%%%%%%%%%%%%%%%%%%%%%%%%%%%%%%%%%%%%%%%%%%%%%%%%%

\begin{document}

% Festlegungen des HARVARD-Zitierstandard
\ifthenelse{\equal{\FHTWCitationType}{HARVARD}}{
\bibliographystyle{Harvard_FHTW_MR}%Zitierstandard FH Technikum Wien, Studiengang Mechatronik/Robotik, Version 1.2e
\citationstyle{dcu}%Correct citation-style (Harvardand, ";" between citations, "," between author and year)
\citationmode{abbr}%use "et al." with first citation
\iflanguage{ngerman}{
    %Deutsch Neue Rechtschreibung
    \newcommand{\citepic}[1]{(Quelle: \protect\cite{#1})}%Zitat: Bild
    \newcommand{\citefig}[2]{(Quelle: \protect\cite{#1}, S. #2)}%Zitat: Bild aus Dokument
    \newcommand{\citefigm}[2]{(Quelle: modifiziert "ubernommen aus \protect\cite{#1}, S. #2)}%Zitat: modifiziertes Bild aus Dokument
    \newcommand{\citep}{\citeasnoun}%In-Line Zitiat entweder mit \citep{} oder \citeasnoun{}
    \newcommand{\acessedthrough}{Verfügbar unter:}%Für URL-Angabe
    \newcommand{\acessedthroughp}{Verfügbar bei:}%Für URL-Angabe (Geschützte Datenbank, Zugriff durch FH)
    \newcommand{\acessedat}{Zugang am}%Für URL-Datum-Angabe
    \newcommand{\singlepage}{S.}%Für Seitenangabe (einzelne Seite)
    \newcommand{\multiplepages}{S.}%Für Seitenangabe (mehrere Seiten)
    \newcommand{\chapternr}{K.}%Für Kapitelangabe
    \renewcommand{\harvardand}{\&}%Harvardand in Zitaten
    \newcommand{\abstractonly}{ausschließlich Abstract}
    \newcommand{\edition}{. Auflage}%Angabe der Auflage
}{
\iflanguage{german}{
    %Deutsch
    \newcommand{\citepic}[1]{(Quelle: \protect\cite{#1})}%Zitat: Bild
    \newcommand{\citefig}[2]{(Quelle: \protect\cite{#1}, S. #2)}%Zitat: Bild aus Dokument
    \newcommand{\citefigm}[2]{(Quelle: modifiziert "ubernommen aus \protect\cite{#1}, S. #2)}%Zitat: modifiziertes Bild aus Dokument
    \newcommand{\citep}{\citeasnoun}%In-Line Zitiat entweder mit \citep{} oder \citeasnoun{}
    \newcommand{\acessedthrough}{Verfügbar unter:}%Für URL-Angabe
    \newcommand{\acessedthroughp}{Verfügbar bei:}%Für URL-Angabe (Geschützte Datenbank, Zugriff durch FH)
    \newcommand{\acessedat}{Zugang am}%Für URL-Datum-Angabe
    \newcommand{\singlepage}{S.}%Für Seitenangabe (einzelne Seite)
    \newcommand{\multiplepages}{S.}%Für Seitenangabe (mehrere Seiten)
    \newcommand{\chapternr}{K.}%Für Kapitelangabe
    \renewcommand{\harvardand}{\&}%Harvardand in Zitaten
    \newcommand{\abstractonly}{ausschließlich Abstract}
    \newcommand{\edition}{. Auflage}%Angabe der Auflage
}{
    %Englisch
    \newcommand{\citepic}[1]{(Source: \protect\cite{#1})}%Zitat: Bild
    \newcommand{\citefig}[2]{(Source: \protect\cite{#1}, p. #2)}%Zitat: Bild aus Dokument
    \newcommand{\citefigm}[2]{(Source: taken with modification from \protect\cite{#1}, p. #2)}%Zitat: modifiziertes Bild aus Dokument
    \newcommand{\citep}{\citeasnoun}%In-Line Zitiat entweder mit \citep{} oder \citeasnoun{}
    \newcommand{\acessedthrough}{Available at:}%Für URL-Angabe
    \newcommand{\acessedthroughp}{Available through:}%Für URL-Angabe (Geschützte Datenbank, Zugriff durch FH)
    \newcommand{\acessedat}{Accessed}%Für URL-Datum-Angabe
    \newcommand{\singlepage}{p.}%Für Seitenangabe (einzelne Seite)
    \newcommand{\multiplepages}{pp.}%Für Seitenangabe (mehrere Seiten)
    \newcommand{\chapternr}{Ch.}%Für Kapitelangabe
    \renewcommand{\harvardand}{\&}%Harvardand in Zitaten
    \newcommand{\abstractonly}{Abstract only}
    \newcommand{\edition}{~edition}%Edition -> note, that you have to write "edition = {2nd},"!
}}}

% Formelverzeichnis
\newcommand{\listequationsname}{Formelverzeichnis}
\newlistof{equations}{equ}{\listequationsname}
\newcommand{\equations}[1]{%
\addcontentsline{equ}{equations}{\protect\numberline{\theequation}#1}\par}

\maketitle

%%%%%%%%%%%%%%%%%%%%%%%%%%%%%%%%%%%%%%%%%%%%%%%%%%%%
%%                  MAIN BODY                     %%
%%%%%%%%%%%%%%%%%%%%%%%%%%%%%%%%%%%%%%%%%%%%%%%%%%%%

%%%%%%%%%%%%%%%%%%%%%%%%%%%%%%%%%%%%%%%%%%%%%%%%%%%%
%%         Problem- und Aufgabenstellung          %%
%%%%%%%%%%%%%%%%%%%%%%%%%%%%%%%%%%%%%%%%%%%%%%%%%%%%
\chapter{Problem- und Aufgabenstellung} % Ausgangssituation, Ziele
    
    Die vorliegende Arbeit beschäftigt sich mit der mechatronischen Auslegung eines parallelkinematischen Delta-Roboters um Studierenden die Möglichkeit zu bieten, anwendungsbezogen Kompetenzen im interdisziplinären Gebiet der Ingenieurswissenschaften zu erwerben. Denn obgleich sich die heutige, schnelllebige Welt und ihre Wirtschaftssysteme rasant verändern, hat die öffentliche Bildung seit ihrer Einführung nahezu dasselbe System beibehalten. Allerdings ist durch den stetig wachsenden Einfluss technologiebezogener Branchen der Erwerb technologischer Kompetenzen, durch die Integration von Ingenieurwissenschaften in den Lehrplan, ein Schlüsselelement für den Erfolg künftiger Studentengenerationen \cite{Eg14}.\\
    \\
    Aktuellen Bildungslehrplänen mangelt es jedoch häufig an Möglichkeiten, um erforderliche Fähigkeiten zu vermitteln \cite{IFR18}. Trotz weltweiter Bestrebungen von Bildungsreformen versucht ein Großteil des derzeitigen Lehrsystems weiterhin, Auszubildende auf die Zukunft vorzubereiten, indem Methoden der Vergangenheit angewandt werden \cite{Eg14}. Um Qualifikationslücken zu schließen, stellt die Bildungsrobotik in Verbindung von Theorien des Konstruktivismus und des Konstruktionismus wertvolle Prinzipien, Methoden und Prozesse zur Verfügung, um technologische Kompetenzen und Fähigkeiten wie logisches, abstraktes und algorithmisches Denken, Analysieren und Handeln zu erwerben \cite{Eg16,ToLa16}.\\
    \\
    Die Auslegung paralleler Strukturen ist für Laien aufgrund der Komplexität parallel ablaufender Bewegungsvorgänge oftmals nur schwer nachvollziehbar. Für die Beschreibung der Kinematik und Dynamik sind ein grundlegendes Verständnis der linearen Algebra und  Kenntnisse über Matrixoperationen im dreidimensionalen Raum notwendig. Dabei erschweren zusätzlich nichtlineare und gekoppelte Bewegungen die Modellierung der Mechanik.\\
    \\
    Das Ziel der Arbeit ist die Auslegung und Konstruktion eines Delta-Roboters für Untersuchungen der inversen Kinematik in der Forschung und Lehre. Infolgedessen soll ein Einstieg in das interdisziplinäre Gebiet der Auslegung und Modellierung paralleler Roboter geschaffen werden. Hierdurch wird die Intention verfolgt, Auszubildenden ingenieurwissenschaftliche Kompetenzen näherzubringen, indem theoretisch erlangtes Wissen praktisch angewandt wird. Der entworfene Roboter muss im Betriebszustand die Sicherheit für Mensch und Maschine gewährleisten, während aufgrund wechselnder Räumlichkeiten der Aufbau portabel gestaltet sein muss. Daraus resultieren Anforderungen einer möglichst kompakten als auch eigensicheren, robusten Konstruktion, welche dennoch möglichst kostengünstig gefertigt werden soll.

%%%%%%%%%%%%%%%%%%%%%%%%%%%%%%%%%%%%%%%%%%%%%%%%%%%%
%%                   Einleitung                   %%
%%%%%%%%%%%%%%%%%%%%%%%%%%%%%%%%%%%%%%%%%%%%%%%%%%%%
\chapter{Einleitung} % Einführung in die Thematik

    %%%%%%%%%%%%%%%%%%%%%%%%%%%%%%%%%%%%%%%%%%%%%%%%%%%%
    %%                 SMART ENGINES                  %%
    %%%%%%%%%%%%%%%%%%%%%%%%%%%%%%%%%%%%%%%%%%%%%%%%%%%%
    Robotik und Automatisierung revolutionieren zusammen mit ''Smart Manufacturing'' gegenwärtig nahezu die gesamte moderne Fertigungsindustrie \cite{FrDe18,TaQi19}. Die erschlossenen Technologien stellen in vielen Bereichen, darunter der automatisierten Fertigung, der Medizin und dem Gesundheitswesen, der Altenpflege und Rehabilitation, der unbemannten Suche und Rettung sowie der Automobilindustrie bereits etablierte Systeme dar \cite{Eg14,SaDa18}. Schon mit derzeitigen Verfahrensweisen sind Roboter in der Lage, zahlreiche Aufgaben effizienter und konsistenter zu erledigen als konventionelle Fertigungsprozesse mit menschlicher Belegschaft \cite{FrDe18}.\\
    \\
    ''Smart Manufacturing'' erfordert die Interaktion, Integration und Fusion physischer und informatischer, softwaretechnischer Komponenten. Dies wird einerseits durch die rasante Weiterentwicklung innovativer Technologien, wie dem Internet of Things (IoT, deutsch: Internet der Dinge), Cloud Computing, respektive der Datenverarbeitung in einer zentralen Cloud, Big Data und deren Analysen und andererseits durch national fortschrittliche Fertigungsstrategien mit dem Ziel einer automatisierten Industrie, wie Industrial Internet, Industrie 4.0 und Made in China 2025, unterstützt \cite{TaQi19}.\\
    \\
    Aktuelle Trendkonzepte verfolgen das gemeinsame Ziel einer ''Smart Factory'', in der cyber-physische Systeme die physischen Prozesse der Fabrik überwachen und dezentrale Entscheidungen treffen. Im Zuge dessen gewinnen ''smarte'' Antriebe mit kontinuierlicher Überwachung des eigenen Zustands, Kommunikation untereinander, dezentraler Datenverarbeitung über Edge-Computing und dem Übertragen von Nutzdaten und relevanten Informationen in eine Cloud immer mehr an Bedeutung.\\
    \\
    Diese vernetzten Systeme ermöglichen die frühzeitige Vorhersage von Fehlern, ergreifen notwendige Korrekturmaßnahmen und können somit rechtzeitig Ausrüstungs- und Prozessausfälle in der Industrie vermeiden. Obwohl Elektromotoren den Großteil der Antriebsmaschinen in dynamischen Systemen der modernen Industrie darstellen, beinhalten diese noch meist ungenutztes Potenzial als ''smarte'' Antriebe ausgeführt zu werden, um Produktivitäts- und Wirkungsgraddaten zu generieren \cite{DoBh18}.
    %%%%%%%%%%%%%%%%%%%%%%%%%%%%%%%%%%%%%%%%%%%%%%%%%%%%
    %%                     HEBI                       %%
    %%%%%%%%%%%%%%%%%%%%%%%%%%%%%%%%%%%%%%%%%%%%%%%%%%%%
    Die in der vorliegenden Arbeit verwendeten Modelle der kommerziell erwerbbaren, modularen Roboterantriebe HEBI X5-1 der Firma HEBI Robotics verfolgen dieses Konzept der ''smarten'' Aktoren. Die vom Hersteller umfassend zur Verfügung gestellte, gut dokumentierte Software und eine eigens entwickelte Programmierschnittstelle (API von engl. Application Programming Interface) für MathWorks\textregistered\ MATLAB (von engl. MATrix LABoraty), ROS (von engl. Robot Operating System), einem in der Forschung etabliertem Software-Framework für Roboteranwendungen, und C/C++ zur Steuerung der Aktuatoren, helfen bei der Inbetriebnahme und dem Bedienen der Module. \\ % \cite{Ka18}.\\
    \\
    Die HEBI X5-1 Antriebe stellen mit maximalem Spitzendrehmoment von 2,5 $[Nm]$, kontinuierlichem Drehmoment von 1,3 $[Nm]$ sowie maximaler Geschwindigkeit von 90 $[\frac{U}{min}]$ die kleinsten Ausführungen der X-Serie dar. Die passiven Schnittstellen der Module dienen zur Energieversorgung sowie zur Kommunikation über 10/100 $[Mbps]$ Ethernet mit Standard Kommunikationsprotokollen \cite{He18}. Diese Schnittstellen ermöglichen zudem externe Geräte wie Kameras oder Endeffektoren zur Manipulation anzuschließen \cite{AnWh17}. Die Sensoren der Aktuatoren ermöglichen eine kontrollierbare Positions-, Geschwindigkeits- und Drehmomentsteuerung sowie eine dreiachsige Trägheitsmessung über eine kostengünstige, dennoch zuverlässige inertiale Messeinheit (IMU von engl. Inertial Measurement Unit), welche mehrere Inertialsensoren kombiniert \cite{He18}.\\
    \\
    Die derzeit im konventionellen Handel erhältlichen Robotersysteme sind bereits in der Lage einen Großteil des Anwendungsgebietes für Manipulatoren abzudecken. Die modulare Struktur der HEBI Antriebe erweitert diesen Bereich allerdings um die Möglichkeit dynamische Konfigurationen bei Anforderungsänderung durchzuführen, um individuell auf spezielle Aufgaben angepasst zu werden. Dies erleichtert für Ingenieure die Entwicklung von Robotern, da das System schnell und kostengünstig moduliert werden kann, welches sich gleichzeitig durch optimales Design auf eine bestimmte Aufgabe spezialisieren lässt. Infolgedessen wird schnelles Redesign und Prototyping erleichtert und unterstützt.\\
    \\
    %%%%%%%%%%%%%%%%%%%%%%%%%%%%%%%%%%%%%%%%%%%%%%%%%%%%
    %%              Educational Robotics              %%
    %%%%%%%%%%%%%%%%%%%%%%%%%%%%%%%%%%%%%%%%%%%%%%%%%%%%
    Darüber hinaus richten sich die Module jedoch auch an Forscher und Lehrende, da durch die zunehmende Verbreitung und Kombination modularer Hardware und Open-Source-Software weder spezielles industrielles Equipment noch Forschungseinrichtungen vonnöten sind, um praxisorientierte Lehrinhalte zu vermitteln und Forschungsmöglichkeiten zu bieten. Forschungsarbeiten werden bei Delta-Robotern in den allgemeinen Bereichen der Kinematik, der Dynamik, der Steuerung, der Konfiguration, des Arbeitsbereichs, der Kalibrierung und der mechanischen Struktur bereits intensiv durchgeführt \cite{BrCo15}. Fortschrittliche Rapid Prototyping Methoden und innovative additive Fertigungsverfahren wie 3D-Druck, mit dem es bereits nahezu in jeder Forschungseinrichtung möglich ist Freiformteile auf Anfrage zu erzeugen, ermöglichen die kostengünstige Entwicklung individueller Roboter \cite{KrWa15,He18}. Zudem erlaubt die schnelle Anpassbarkeit an spezifische Aufgabenstellungen, durch die Wiederverwendbarkeit von Hardware- und Software-Modulen, Robotersysteme skalierbarer Komplexität und ermöglicht somit eine neue, adäquate Form Auszubildenden Lehrinhalte zu vermitteln.\\
    \newpage
    \noindent
    Im nachfolgenden Kapitel \ref{cap:stand-der-technik} wird ein Überblick über den Stand der Technik parallelkinematischer Industrieroboter gegeben. Kapitel \ref{cap:geometrische-modellierung} erläutert die geometrische Modellierung des Systems. Kapitel \ref{cap:mathematische-modellierung} beschreibt die Grundlagen der mathematischen Modellierung des Systems mit Berechnung der inversen Kinematik und stellt nachfolgend die Jacobi-Matrix vor. 
    % Diese beschreibt den Zusammenhang zwischen den Gelenkgeschwindigkeiten und der Geschwindigkeit des Endeffektors und wird für analytische Lösungsverfahren der inversen Kinematik bei beliebigen Robotertypen herangezogen. 
    In Kapitel \ref{cap:ergebnisse} werden die Ergebnisse der Arbeit in der Auslegung der Hardware und Entwicklung der Software präsentiert. Anschließend wird in Kapitel \ref{cap:zusammenfassung-und-ausblick} die Arbeit zusammengefasst und ein Ausblick gegeben. Den Abschluss bildet Kapitel \ref{cap:diskussion} indem die Ergebnisse diskutiert und Verbesserungspotenziale beleuchtet werden.

%%%%%%%%%%%%%%%%%%%%%%%%%%%%%%%%%%%%%%%%%%%%%%%%%%%%
%%                Stand der Technik               %%
%%%%%%%%%%%%%%%%%%%%%%%%%%%%%%%%%%%%%%%%%%%%%%%%%%%%
\chapter{Stand der Technik}
\label{cap:stand-der-technik}
    
    %%%%%%%%%%%%%%%%%%%%%%%%%%%%%%%%%%%%%%%%%%%%%%%%%%%%
    %%                  Delta-Roboter                 %%
    %%%%%%%%%%%%%%%%%%%%%%%%%%%%%%%%%%%%%%%%%%%%%%%%%%%%
    Die Mehrzahl der derzeit eingesetzten Industrieroboter sind aus seriellen oder parallelen kinematischen Mechanismen aufgebaut \cite{SiKh16}. Im Allgemeinen besteht eine räumliche mechanische Struktur aus starren Körpern, sogenannten Gliedern, welche über Gelenke miteinander verbunden werden, um eine Relativbewegung zwischen benachbarten Gliedern zu ermöglichen \cite{LyPa17}.\\
    \\
    Ein Robotermechanismus mit serieller, offener kinematischer Kette besteht aus einer Reihe aktiver Gelenke, welche die Basis mit dem Endeffektor verbindet. Alle Bewegungsachsen des Systems sind nacheinander angeordnet und jede zusätzliche Achse ergänzt den Mechanismus um einen weiteren Freiheitsgrad (DoF von engl. Degree of Freedom). Dadurch wird jedoch auch jeder Antrieb mit den Massen der nachfolgenden Glieder und Antriebe belastet \cite{Ne06}.\\
    \\
    Dementgegen wird bei einer parallelen, geschlossenen kinematischen Kette nur eine Teilmenge der Gelenke aktiv betätigt \cite{LyPa17}. Parallele Strukturen haben keine im geometrischen Sinne parallelen Baugruppen, die Terminologie bezieht sich auf die in die Struktur integrierten Parallelogramme \cite{Ne06}. Parallelroboter verfügen im Allgemeinen über eine invariante Basis welche fix mit dem Referenzrahmen verbunden ist, sowie eine bewegliche Plattform mit angebrachtem Endeffektor. Dieser ist über mindestens zwei unabhängige kinematische Ketten mit der festen Basis verbunden und somit in der Lage mit \textit{n} Freiheitsgraden arbiträre Bewegungen im Arbeitsraum durchzuführen \cite{SiKh16,StCa03}. Der wie ein Parallelogramm aufgebaute Zwischenmechanismus ermöglicht die Pose, respektive die Position und Orientierung der beweglichen Plattform, auf drei rein translatorische Freiheitsgrade zu beschränken. Für die passiven Gelenke konventioneller Parallelroboter werden Kugel-, Dreh- oder Prismengelenke eingesetzt, während die aktiven Gelenke meist als Rotations- oder Lineargelenke ausgeführt werden \cite{StCa03}.\\
    \\
    Die gängiste Konstruktionsvariante paralleler Strukturen und der mit Abstand erfolgreichste Parallelroboter für industrielle Anwendungen wurde von \textit{Reymond Clavel} in den frühen 1980er Jahren entwickelt und ist unter dem Namen Delta-Roboter bekannt \cite{Cl90,CrLe17,SoVa18}. Der Roboter wurde für den industriellen Einsatz mit dem Ziel sehr leichte Objekte möglichst schnell zu manipulieren entwickelt, um den monotonen, manuellen Verpackungsprozess von Schokoladenpralinen zu automatisieren. \cite{BrCo15} Die aus diesem Konzept entstandenen parallelkinematischen Mechanismen heben sich besonders durch ihr im Vergleich zu etablierten Industrierobotern hohes Last-Gewicht-Verhältnis sowie die hohe Wiederholgenauigkeit und Steifigkeit, welche auf die parallelverkettete Kinematik zurückzuführen sind, ab. Zudem ist die Fertigung durch den identen Aufbau der kinematischen Ketten kostengünstig. Darüber hinaus erlangen Delta-Roboter hohe dynamische Leistungen, da die schweren Antriebe und Getriebe auf der invarianten Basis montiert sind und diese, durch Einsatz von leichten Verbundwerkstoffen für die Glieder, nur relativ geringe Massen bewegen müssen. Resultierend sind Delta-Strukturen prädestiniert schnell hohe Beschleunigungen erreichen zu können. Ein Nachteil im Vergleich mit seriellen Roboterstrukturen ist jedoch etwa das im Verhältnis zum Bauraum relativ eingeschränkte Arbeitsraumvolumen und die anspruchsvolle Auslegung des Roboters \cite{Ne06}.\\
    \\
    Neben zahlreichen Abwandlungen der ursprünglichen Architektur finden, besonders im industriellen Umfeld, Delta-Roboter mit Rotations- oder Linearantrieben Einsatz. Sind sowohl die Rotations- als auch die proximalen Gelenke durch Lineargelenke ersetzt, wird dieser Robotertyp oft als ''Linapod'' oder ''linearer Delta-Roboter'' bezeichnet.  Delta-Roboter werden oftmals zusätzlich mit seriellen Mechanismen erweitert, um hybridkinematische Strukturen mit weiteren Freiheitsgraden zu erreichen und somit etwa auch die Orientierung des Werkstückes, wie bei den meisten Montage- und Bestückungsanwendungen erforderlich, perpendikular zum Endeffektor beeinflussen zu können \cite{BrCo15}. Obwohl das industrielle Einsatzgebiet von Hochgeschwindigkeits-Bestückungs- und Verpackungsanwendungen im Lebensmittel- und Medizinsektor bis hin zu Montageanwendungen, Einsatz im elektronischen Sektor, wie etwa der Photovoltaikindustrie, als Laser Cutter oder 3D-Drucker reicht, entsprach der weltweite Marktanteil im Jahr 2012 von Parallelrobotern nur rund 1 $[\%]$, da das Anwendungsgebiet durch das beschränkte Arbeitsraumvolumen der Roboter relativ eingegrenzt ist \cite{BrCo15}. In Tabelle \ref{tab:gegenüberstellung-seriell-paralell} ist abschließend eine zusammenfassende Gegenüberstellung serieller und pralleler Strukturen dargestellt.
    \begin{table}[H]
        \centering
        \caption{Vergleich der Eigenschaften von Seriell- und Parallelkinematiken \citefigm{PaDu14}{157}}\label{tab:gegenüberstellung-seriell-paralell}
            \begin{tabular}{| p{5.7cm} | C{4.5cm} | C{4.5cm} |}\hline 
                \rowcolor[gray]{0.8} Merkmal & Serielle Struktur & Parallele Struktur\\\hline
                Arbeitsbereich & Groß & Klein und komplex\\\hline
                Lösen der direkten Kinematik & Einfach & Sehr schwierig\\\hline 
                Lösen der inversen Kinematik & Schwierig & Einfach\\\hline 
                Positionsfehler & Akkumuliert & Mittelwert\\\hline
                Kraftfehler & Mittelwert & Akkumuliert\\\hline
                Maximale Kraft & Begrenzt durch minimale Aktuatorkraft & Summe aller Aktuatorkräfte\\\hline
                Steifigkeit & Niedrig & Hoch\\\hline
                Dynamikeigenschaften & Niedrig & Sehr hoch\\\hline 
                Modellierungs- und \newline Lösungsdynamik & Relativ einfach & Sehr komplex\\\hline
                Trägheit & Groß & Klein\\\hline
                Anwendungsbereiche & Große Anzahl & Relativ begrenzt\\\hline
                Nutzlast- zu Gewichtsverhältnis & Niedrig & Hoch\\\hline
                Geschwindigkeit und \newline Beschleunigung & Niedrig & Hoch\\\hline
                Genauigkeit & Niedrig & Hoch\\\hline
                Gleichmäßigkeit der \newline Komponenten & Niedrig & Hoch\\\hline
                Kalibrierung & Relativ einfach & Kompliziert\\\hline
                Arbeits- zu Bauraum & Groß & Klein\\\hline
                % Genauigkeit & - & +\\\hline
                % Steuerungsaufwand & + & -\\\hline
                % Objekt- zu Maschinenmasse & - & +\\\hline
                % Größe des Arbeitsraums & + & -\\\hline
                % Beschleunigung am Endeffektor & - & +\\\hline
                % Anpassbarkeit an Aufgabenstellung & + & -\\\hline
                % Struktursteifigkeit & - & +\\\hline
                % Trägheitskräfte & - & +\\\hline
                % Messfehler in der Struktur & addierend & mittelwertbildend\\\hline
                % Arbeits- zu Bauraum & + & -\\\hline
                % Beweglichkeit im Arbeitsraum & + & -\\\hline
                % Kalibration & + & -\\\hline
            \end{tabular}
    \end{table}
    % \newline
    \noindent

% \chapter{Systematische Vorgehensweise}
% \chapter{Entwicklung und Evaluierung der Konzepte}

%%%%%%%%%%%%%%%%%%%%%%%%%%%%%%%%%%%%%%%%%%%%%%%%%%%%
%%     Geometrische Modellierung des Systems      %%
%%%%%%%%%%%%%%%%%%%%%%%%%%%%%%%%%%%%%%%%%%%%%%%%%%%%
\newpage
\chapter{Geometrische Modellierung des Systems}
\label{cap:geometrische-modellierung}

    Abbildung \ref{fig:delta-denotation} zeigt die geschlossene kinematische Kette des Delta-Roboters mit drei translatorischen Freiheitsgraden. Der entworfene Prototyp basiert auf drei identischen, parallelverketteten Strukturen zwischen der oberen invarianten Basis und unteren beweglichen Plattform. Die topologische Struktur einer dieser Ketten besteht aus einem auf der Basis (1) montierten Antrieb mit aktivem Rotationsgelenk, einem parallelen Zwischenmechanismus mit proximalem (2) und distalem (3) Glied, welches über abschließende, passiv sphärische Verbindungen mit dem proximalen Glied und der beweglichen Plattform (4) verbunden ist. Da die distalen Glieder, im Gegensatz zu den proximalen Gliedern, nur axiale Kräfte übertragen müssen, können für diese leichte Materialien verwendet werden, resultierend in einer sehr geringen Trägheit der distalen Glieder.\\
    \begin{figure}[H]
        \centering
        %\fbox
        {
            
        }
        \caption[Grundlegende Struktur mit Notation des Delta-Roboters]{Grundlegende Struktur mit Notation des Delta-Roboters \citefigm{Zs04}{8}}
        \label{fig:delta-denotation}
    \end{figure}
    % \newline
    \noindent
    Die linke Seite der Abbildung \ref{fig:top-view} zeigt eine Draufsicht der invarianten Basis mit dem im Zentrum liegenden Koordinatensystem $O = \bigl[ \begin{smallmatrix} x_o & y_o & z_o \end{smallmatrix} \bigr]^{\mathsmaller T}$. Im jeweiligen Mittelpunkt der drei Seiten des von der Basis aufgespannten Dreiecks liegen die drei Punkte $F_i$ ($i = 1, 2, 3)$, welche der Position der Aktoren entsprechen, an denen die kinematischen Ketten mit der Basis verbunden sind. Die Länge $R$ ist der Inkreisradius sowie der Abstand eines Aktors $F_i$ zum Urspung $O$. Die rechte Seite der Abbildung veranschaulicht eine Draufsicht der beweglichen Plattform. Die drei Eckpunkte des aufgespannten Dreiecks $E_i$, mit dem Umkreisradius $r$ vom Punkt $P$ entfernt, beschreiben die Positionen der abschließenden, passiv sphärischen Verbindungen, welche die kinematischen Ketten mit der beweglichen Plattform verbinden.
    \begin{figure}[H]
        \centering
        %\fbox
        {
            
        }
        \caption[Draufsicht mit Notation der invarianten Basis (links) und beweglichen Plattform (rechts) des Delta-Roboters]{Draufsicht mit Notation der invarianten Basis (links) und beweglichen Plattform (rechts) des Delta-Roboters}
        %\citefigm{Wi16}
        \label{fig:top-view}
    \end{figure}
    % \newline
    \noindent
    Da sich sowohl die aktiven Gelenkkoordinaten der invarianten Basis $F_i$ sowie die passiven Gelenkkoordinaten der beweglichen Plattform $E_i$ auf In- bzw. Umkreisen mit Mittelpunkt in den Punkten $O$ und $P$ sowie den Radii $R$ und $r$ befinden, und die Winkelabstände der aktiven und passiven Gelenke zueinander um die Applikaten ident sind, kann eine Rotationsmatrix eingeführt werden, um aus dem globalen Basiskoordinatensystem $O$ in die lokalen, gliederseitigen Koordinatensysteme $F_i$ zu gelangen:
    \begin{align}
        ^iT_O = 
            \left[
                \begin{array}{c c c} 
                    cos(\alpha) & - sin(\alpha) & 0 \\ 
                    sin(\alpha) & cos(\alpha) & 0 \\
                    0 & 0 & 1
                \end{array}
            \right]
        \label{eq:transformationsmatrix}
    \end{align}
    \equations{Formel \ref{eq:transformationsmatrix} Transformationsmatrix}
    \noindent
    Die linke Seite der Abbildung \ref{fig:delta-closed-loop} zeigt die Seitenansicht der Kinematik einer geschlossenen Kette des Delta-Roboters. Die Notation ist einheitlich zu Abbildung \ref{fig:top-view} und wird um die Länge des proximalen Gliedes $a$, die des distalen $b$, deren Winkel $\theta\textsubscript{1i}$ und $\theta\textsubscript{2i}$ sowie den Abstand $p$ zwischen dem Zentrum der beweglichen Plattform $P$ und der invarianten Basis $O$ erweitert. Um die parallele Struktur der Zwischenmechanik zu verdeutlichen, sowie den Winkel $\theta\textsubscript{3i}$ definieren zu können, veranschaulicht die rechte Seite der Abbildung die analoge Kinematik einer geschlossenen Kette, -90 $[^{\circ}]$ um $z_o$ gedreht. Das kartesische Koordinatensystem $O$ wird so definiert, dass die  von der Abszisse und Ordinate aufgespannte Ebene mit der Ebene der invarianten Basis kongruiert.
    \begin{figure}[H]
        \centering
        %\fbox
        {
            
        }
        \caption[{Seitenansicht mit Notation der Kinematik einer geschlossenen Kette des Delta-Roboters (links), analoge Kette, -90 $[^{\circ}]$ um $z_o$ gedreht (rechts)}]{Seitenansicht mit Notation der Kinematik einer geschlossenen Kette des Delta-Roboters (links), analoge Kette, -90 $[^{\circ}]$ um $z_o$ gedreht (rechts)}
        % \citefigm{LyPa17}
        \label{fig:delta-closed-loop}
    \end{figure}
    % \newline
    \noindent
    Der Zustand des physikalischen Systems wird durch den Vektor $\vv{\theta}$ bestehend aus den aktiven Gelenkvariablen, respektive den generalisierten Koordinaten, eindeutig festlegt 
    \begin{align}
        \vv{\theta} \equiv \vv{\theta\textsubscript{1i}} = 
            \left[
                \begin{array}{c} 
                    \theta\textsubscript{11} \\ 
                    \theta\textsubscript{12} \\ 
                    \theta\textsubscript{13} 
                \end{array}
            \right]
        \label{eq:aktive_gelenkvariablen}
    \end{align}
    \equations{Formel \ref{eq:aktive_gelenkvariablen} Aktive Gelenkvariablen}
    \noindent
    zudem wird die Position der beweglichen Plattform über den Vektor $\vv{p}$ definiert
    \begin{align}
        \vv{p} = 
            \left[
                \begin{array}{c} 
                    x_p\\
                    y_p\\
                    z_p 
                \end{array}
            \right]
        \label{eq:tcp}
    \end{align}
    \equations{Formel \ref{eq:tcp} Vektor TCP}
    \noindent

%%%%%%%%%%%%%%%%%%%%%%%%%%%%%%%%%%%%%%%%%%%%%%%%%%%%
%%     Mathematische Modellierung des Systems     %%
%%%%%%%%%%%%%%%%%%%%%%%%%%%%%%%%%%%%%%%%%%%%%%%%%%%%
% \newpage
\chapter{Mathematische Modellierung des Systems}
\label{cap:mathematische-modellierung}

    \section{Kinematik}
    
    Die Kinematik beschreibt Stellungen, Geschwindigkeiten und Beschleunigungen der Gelenke in Relation zu den Bewegungen des Endeffektors und bildet somit die Grundlage für diverse Untersuchungen. Die Bewegungslehre kann in zwei mathematische Modellierungen, der direkten und der inversen Kinematik, unterschieden werden.\\
    \\
    Die direkte Kinematik definiert die Pose des Endeffektors bei gegebenen Gelenkwinkeln, während die inverse Kinematik bei bekannter Pose des Endeffektors die entsprechenden Gelenkwinkel liefert. Somit wird die inverse Kinematik in Anwendungen, in denen die Zielposen des Endeffektors vorgegeben sind und die Sollwerte der Gelenke berechnet werden sollen, etwa bei Pick-and-Place Aufgaben, verwendet, da die hiermit ermittelten Werte in weiterer Folge der Steuerung zur Trajektorienplanung übergeben werden können. Zur Berechnung der inversen Kinematik gibt es verschiedene Herangehensweisen, etwa einen regelbasierten Ansatz, ein numerisches Verfahren, welches sich der inversen \textit{Jacobi-Matrix} bedient sowie ein algebraisches und auch geometrisches, analytisches Lösungsverfahren \cite{We08}. Letzteres beschreibt die in der Arbeit umgesetzte Methodik. 

    \section{Bestimmung der Freiheitsgrade des Systems}
    \label{sec:DoF}
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

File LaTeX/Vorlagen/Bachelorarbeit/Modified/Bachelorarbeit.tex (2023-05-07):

%
% FH Technikum Wien
% !TEX encoding = UTF-8 Unicode
%

\documentclass[Bachelor, BMR, ngerman]{twbook}
\usepackage[utf8]{inputenc}
\usepackage[T1]{fontenc}

% --------------------------------------------------
% CITE
% --------------------------------------------------
\newcommand{\FHTWCitationType}{HARVARD} 
\ifthenelse{\equal{\FHTWCitationType}{HARVARD}}{\usepackage{harvard}}{\usepackage{bibgerm}}

% --------------------------------------------------
% FORMAT CODE LISTINGS
% --------------------------------------------------
\usepackage[final]{listings}
\lstset{captionpos=b, numberbychapter=false,caption=\lstname,frame=single, numbers=left, stepnumber=1, numbersep=2pt, xleftmargin=15pt, framexleftmargin=15pt, numberstyle=\tiny, tabsize=3, columns=fixed, basicstyle={\fontfamily{pcr}\selectfont\footnotesize}, keywordstyle=\bfseries, commentstyle={\color[gray]{0.33}\itshape}, stringstyle=\color[gray]{0.25}, breaklines, breakatwhitespace, breakautoindent}
\lstloadlanguages{[ANSI]C, C++, [gnu]make, gnuplot, Matlab}
\makeatletter
\providecommand\listacroname{}
\@ifclasswith{twbook}{english}
{%
    \renewcommand\lstlistingname{Code}
    \renewcommand\lstlistlistingname{List of Code}
    \renewcommand\listacroname{List of Abbreviations}
}{%
    \renewcommand\lstlistingname{Quellcode}
    \renewcommand\lstlistlistingname{Quellcodeverzeichnis}
    \renewcommand\listacroname{Abkürzungsverzeichnis}
}
\newcommand\listoflolentryname\lstlistingname
\makeatother
\newcommand{\listofcode}{\phantomsection\lstlistoflistings}

% --------------------------------------------------
%  AUXILARY PACKAGES
% --------------------------------------------------
\usepackage{blindtext}
\usepackage{colortbl} % Für farbige Tabellen
%\usepackage{media9}

% --------------------------------------------------
% TITLE & AUTHOR
% --------------------------------------------------
\title{Konstruktion eines Delta Roboters zur Untersuchung der inversen Kinematik }
\author{Felix Schausberger}
\studentnumber{mr16b049}
%\author{Titel Vorname Name, Titel\and{}Titel Vorname Name, Titel}
%\studentnumber{XXXXXXXXXXXXXXX\and{}XXXXXXXXXXXXXXX}
\supervisor{Mohammed Aburaia, MSc}
%\supervisor[Begutachter]{Titel Vorname Name, Titel}
%\supervisor[Begutachterin]{Titel Vorname Name, Titel}
%\secondsupervisor{Titel Vorname Name, Titel}
%\secondsupervisor[Begutachter]{Titel Vorname Name, Titel}
%\secondsupervisor[Begutachterinnen]{Titel Vorname Name, Titel}
\place{Wien}

% --------------------------------------------------
% KURZFASSUNG, ABSTRACT & KEYWORDS
% --------------------------------------------------
\kurzfassung{
    Projektziele: 
    \begin{itemize}
        \item Realisierung einer Deltakinematik.
        \item Implementierung einer Pick-and-Place-Applikation mit vollst{\"a}ndiger Beschreibung der inversen Kinematik einer geschlossenen kinematischen Kette.
        \item Modularer Aufbau, alle Verbindungen werden gesteckt oder geschraubt.
        \item Einhausung des Roboters mit 20 [mm] Aluprofilrahmen.
        \item Die aktiven Gelenke des Roboters werden mit Hebi X5-1 Motoren realisiert.
        \item Die passiven Gelenke des Roboters werden mit Doppelgelenklager realisiert.
    \end{itemize}
    Das Ziel der Arbeit ist eine vollständige Beschreibung der inversen Kinematik eines Delta Roboters um bei Studierenden die Lehrinhalte aus der Lehrveranstaltung AURO zu festigen und praktisch anzuwenden. 
    Lernziele der Studierenden: Freiheitsgrade, TCP, Lage der Antriebe, zeichnen kinematischer Ketten, Pose, festlegen von Koordinatensystemen mit DH-Notation, berechnen der inverse Kinematik einer geschlossenen kinematischen Kette mit Anwendung von Rotations- und Transformationsmatrizen sowie der Jacobi Matrix.
    }
\schlagworte{Parallelkinematik, geschlossene kinematische Kette, inverse Kinematik, Delta Roboter, smart engines}
% \outline{\blindtext}
% \keywords{Keyword1, Keyword2, Keyword3, Keyword4}
%\acknowledgements{\blindtext}

%%%%%%%%%%%%%%%%%%%%%%%%%%%%%%%%%%%%%%%%%%%%%%%%%%%%
%%                 BEGIN DOCUMENT                 %%
%%%%%%%%%%%%%%%%%%%%%%%%%%%%%%%%%%%%%%%%%%%%%%%%%%%%

\begin{document}

%Festlegungen für den HARVARD-Zitierstandard
\ifthenelse{\equal{\FHTWCitationType}{HARVARD}}{
\bibliographystyle{Harvard_FHTW_MR}%Zitierstandard FH Technikum Wien, Studiengang Mechatronik/Robotik, Version 1.2e
\citationstyle{dcu}%Correct citation-style (Harvardand, ";" between citations, "," between author and year)
\citationmode{abbr}%use "et al." with first citation
\iflanguage{ngerman}{
    %Deutsch Neue Rechtschreibung
    \newcommand{\citepic}[1]{(Quelle: \protect\cite{#1})}%Zitat: Bild
    \newcommand{\citefig}[2]{(Quelle: \protect\cite{#1}, S. #2)}%Zitat: Bild aus Dokument
    \newcommand{\citefigm}[2]{(Quelle: modifiziert "ubernommen aus \protect\cite{#1}, S. #2)}%Zitat: modifiziertes Bild aus Dokument
    \newcommand{\citep}{\citeasnoun}%In-Line Zitiat entweder mit \citep{} oder \citeasnoun{}
    \newcommand{\acessedthrough}{Verfügbar unter:}%Für URL-Angabe
    \newcommand{\acessedthroughp}{Verfügbar bei:}%Für URL-Angabe (Geschützte Datenbank, Zugriff durch FH)
    \newcommand{\acessedat}{Zugang am}%Für URL-Datum-Angabe
    \newcommand{\singlepage}{S.}%Für Seitenangabe (einzelne Seite)
    \newcommand{\multiplepages}{S.}%Für Seitenangabe (mehrere Seiten)
    \newcommand{\chapternr}{K.}%Für Kapitelangabe
    \renewcommand{\harvardand}{\&}%Harvardand in Zitaten
    \newcommand{\abstractonly}{ausschließlich Abstract}
    \newcommand{\edition}{. Auflage}%Angabe der Auflage
}{
\iflanguage{german}{
    %Deutsch
    \newcommand{\citepic}[1]{(Quelle: \protect\cite{#1})}%Zitat: Bild
    \newcommand{\citefig}[2]{(Quelle: \protect\cite{#1}, S. #2)}%Zitat: Bild aus Dokument
    \newcommand{\citefigm}[2]{(Quelle: modifiziert "ubernommen aus \protect\cite{#1}, S. #2)}%Zitat: modifiziertes Bild aus Dokument
    \newcommand{\citep}{\citeasnoun}%In-Line Zitiat entweder mit \citep{} oder \citeasnoun{}
    \newcommand{\acessedthrough}{Verfügbar unter:}%Für URL-Angabe
    \newcommand{\acessedthroughp}{Verfügbar bei:}%Für URL-Angabe (Geschützte Datenbank, Zugriff durch FH)
    \newcommand{\acessedat}{Zugang am}%Für URL-Datum-Angabe
    \newcommand{\singlepage}{S.}%Für Seitenangabe (einzelne Seite)
    \newcommand{\multiplepages}{S.}%Für Seitenangabe (mehrere Seiten)
    \newcommand{\chapternr}{K.}%Für Kapitelangabe
    \renewcommand{\harvardand}{\&}%Harvardand in Zitaten
    \newcommand{\abstractonly}{ausschließlich Abstract}
    \newcommand{\edition}{. Auflage}%Angabe der Auflage
}{
    %Englisch
    \newcommand{\citepic}[1]{(Source: \protect\cite{#1})}%Zitat: Bild
    \newcommand{\citefig}[2]{(Source: \protect\cite{#1}, p. #2)}%Zitat: Bild aus Dokument
    \newcommand{\citefigm}[2]{(Source: taken with modification from \protect\cite{#1}, p. #2)}%Zitat: modifiziertes Bild aus Dokument
    \newcommand{\citep}{\citeasnoun}%In-Line Zitiat entweder mit \citep{} oder \citeasnoun{}
    \newcommand{\acessedthrough}{Available at:}%Für URL-Angabe
    \newcommand{\acessedthroughp}{Available through:}%Für URL-Angabe (Geschützte Datenbank, Zugriff durch FH)
    \newcommand{\acessedat}{Accessed}%Für URL-Datum-Angabe
    \newcommand{\singlepage}{p.}%Für Seitenangabe (einzelne Seite)
    \newcommand{\multiplepages}{pp.}%Für Seitenangabe (mehrere Seiten)
    \newcommand{\chapternr}{Ch.}%Für Kapitelangabe
    \renewcommand{\harvardand}{\&}%Harvardand in Zitaten
    \newcommand{\abstractonly}{Abstract only}
    \newcommand{\edition}{~edition}%Edition -> note, that you have to write "edition = {2nd},"!
}}}

\maketitle

%%%%%%%%%%%%%%%%%%%%%%%%%%%%%%%%%%%%%%%%%%%%%%%%%%%%
%%                  MAIN BODY                     %%
%%%%%%%%%%%%%%%%%%%%%%%%%%%%%%%%%%%%%%%%%%%%%%%%%%%%

\chapter{Einleitung/Einführung in die Thematik}

    Robotik und Automatisierung revolutionieren zusammen mit Smart Manufacturing gegenwärtig nahezu die gesamte moderne Fertigungsindustrie. \cite{FrDe18,TaQi19} Die erschlossenen Technologien stellen in vielen Bereichen, darunter der automatisierten Fertigung, der Medizin und dem Gesundheitswesen, der Altenpflege und Rehabilitation, der unbemannten Suche und Rettung sowie der Automobilindustrie bereits etablierte Systeme dar. \cite{Eg14,SaDa18} Schon mit derzeitigen Verfahrensweisen sind Roboter in der Lage, zahlreiche Aufgaben effizienter und konsistenter zu erledigen als konventionelle Fertigungsprozesse mit menschlicher Belegschaft. \cite{FrDe18}\\
    \\
    Smart Manufacturing erfordert die Interaktion, Integration und Fusion physischer und informatischer, softwaretechnischer Komponenten. Dies wird einerseits durch die rasante Weiterentwicklung innovativer Technologien, wie dem Internet der Dinge (IoT), Cloud Computing, Big Data und deren Analysen, cyber-physischer Systeme sowie mobilen Internet und andererseits durch nationale fortschrittliche Fertigungsstrategien mit dem Ziel einer automatisierten Industrie, wie Industrial Internet, Industrie 4.0 und Made in China 2025, unterstützt. \cite{TaQi19}\\
    \\
    Aktuelle Trendkonzepte verfolgen das gemeinsame Ziel einer "Smart Factory", in der cyber-physische Systeme die physischen Prozesse der Fabrik überwachen und dezentrale Entscheidungen treffen. Im Zuge dessen gewinnen "smarte" Antriebe mit kontinuierlicher Überwachung des eigenen Zustands, Kommunikation untereinander mit Edge-Computing und dem Übertragen von Nutzdaten und relevanten Informationen in eine Cloud immer mehr an Bedeutung.\\
    \\
    Dieses Zusammenspiel ermöglicht, Fehler frühzeitig vorherzusagen, Korrekturmaßnahmen zu ergreifen und somit rechtzeitig Ausrüstungs- und Prozessausfälle in der Industrie zu vermeiden. Obwohl Elektromotoren den Großteil der Antriebsmaschinen in dynamischen Systemen der modernen Industrie darstellen, halten diese noch meist ungenutzes Potential als smarte Antriebe ausgeführt zu werden um Produktivitäts- und Wirkungsgraddaten zu generieren. \cite{DoBh18}

\chapter{Stand der Technik}
    
    Die meisten der derzeit eingesetzten Industrieroboter sind aus seriellen oder parallelen kinematischen Mechanismen aufgebaut \cite{SiKh16}. Im Allgemeinen besteht eine räumliche mechanische Struktur aus starren Körpern, sogenannten Gliedern, welche über Gelenke miteinander verbunden werden, um eine Relativbewegung zwischen benachbarten Gliedern zu ermöglichen \cite{LyPa17}.\\
    \\
    Ein Robotermechanismus mit serieller, offener kinematischen Kette besteht aus einer Reihe aktiver Gelenke, welche die Basis mit dem Endeffektor verbindet. Alle Bewegungsachsen des Systems sind nacheinander angeordnet und jede zusätzliche Achse ergänzt den Mechanismus um einen weiteren Freiheitsgrad.  Dadurch wird jedoch auch jeder Antrieb wird mit den Massen der nachfolgenden Glieder und Antriebe belastet \cite{Ne06}.\\
    \\
    Dementgegen wird bei einer parallelen, geschlossenen kinematischen Kette nur eine Teilmenge der Gelenke aktiv betätigt \cite{LyPa17}.\\ 
    \\
    Diese parallelen Strukturen haben keine im geometrischen Sinne parallelen Baugruppen \cite{Ne06}, die Terminologie bezieht sich auf die in die Struktur integrierten Parallelogramme. Der Einsatz dreier Parallelogramme ermöglicht die Pose\footnote{Respektive die Position und Orientierung.} der beweglichen Plattform auf drei rein translatorische Freiheitsgrade (DoF) zu beschränken. Parallelroboter verfügen im Allgemeinen über eine höhergelegene, invariante Basis welche fix mit dem Referenzrahmen verbunden ist, sowie eine tiefer gelegene, bewegliche Plattform mit angebrachtem Endeffektor. Dieser ist über mindestens zwei unabhängige kinematische Ketten mit der festen Basis verbunden und somit in der Lage mit \textit{n} Freiheitsgraden arbiträre Bewegungen im Arbeitsraum durchzuführen \cite{SiKh16,StCa03}. Hierbei werden konventionell die passiven Gelenke des Roboters mit Kugel-, Dreh- oder Prismengelenken ausgeführt. Für die aktiven Gelenke des Roboters werden meist Rotations- oder Lineargelenke eingesetzt \cite{StCa03}.\\
    \\
    Die gängiste Konstruktionsvariante paraller Strukturen und der mit Abstand erfolgreichste Parallelroboter für industrielle Anwendungen ist der sogenannte Delta Roboter \cite{CrLe17,SoVa18}.\\
    \\
    -> VOTEILE PARALLELROBOTER

\chapter{Optional: Educational Robotics}

    Obwohl sich die heutige, schnelllebige Welt und ihre Wirtschaftssysteme rasant verändern, hat die öffentliche Bildung seit ihrer Einführung nahezu dasselbe System beibehalten. Durch den stetig wachsenden Einfluss technologiebezogener Branchen ist der Erwerb technologischer Kompetenzen durch die Integration von Ingenieurwissenschaften in den Lehrplan ein Schlüsselelement für den Erfolg der nächsten Studentengeneration. \cite{Eg14}\\
    \\
    Aktuellen Bildungslehrplänen für Studenten mangelt es oft an Möglichkeiten, um erforderliche Fähigkeiten zu erwerben. (IFR18) Trotz weltweiter Bestrebungen von Bildungsreformen versucht ein Großteil des derzeitigen Lehrsystems weiterhin, Auszubildende auf die Zukunft vorzubereiten, indem Methoden der Vergangenheit angewandt werden. \cite{Eg14}\\
    \\
    Um Qualifikationslücke zu schließen stellt die Bildungsrobotik in Verbindung von Theorien des Konstruktivismus und des Konstruktionismus wertvolle Prinzipien, Methoden und Prozesse zur Verfügung um technologische Kompetenzen und Fähigkeiten wie logisches, abstraktes und algorithmisches \cite{Eg16} Denken, analysieren und handeln zu erwerben. \cite{ToLa16}\\
    \\
    Schnelle Anpassbarkeit an spezifische Aufgabenstellungen durch die wiederverwendbrkeit von Hardware- und Software-Modulen erlaubt Robotersysteme skalierbarer Komplexität.\\
    Selbst gebaute Roboter sind deshalb so ideal, weil dort das Wissen aus Mechanik, Elektrotechnik und Informatik zu einem System integriert wird und man sofort sieht, ob es funktioniert. Anschaulicher können die Aufgaben eines Ingenieurs nicht vermittelt werden.\\
    Interdisziplinäres Gebiet: Programmierung, Geometrie, Robotik, Ingenieurwesen, Design.

\chapter{Ausgangssituation/Problem- und Aufgabenstellung/Ziele}
\chapter{Systematische Vorgehensweise}
\chapter{Entwicklung und Evaluierung der Konzepte}
\chapter{Modellierung des Systems}
\section{Auslegung der Hardware}

    Abb. 1 zeigt den Prototyp der geschlossenen kinematischen Kette des Delta Roboters mit drei translatorischen Freiheitsgraden. Diese basieren auf drei identischen, parallelverketteten Strukturen zwischen der oberen invarianten Basis und unteren beweglichen Plattform. Die topologische Struktur einer dieser Ketten besteht aus einem auf der Basis (1) montierten Antrieb mit aktivem Drehgelenk (2), einem parallelen Zwischenmechanismus (3) und einer abschließenden passiv drehbaren Verbindung (4), welche mit der beweglichen Plattform (5) verbunden ist. Die aktiven Drehgelenke des Roboters sind über an der Basis montierte Hebi X5-1 Antriebe ausgeführt. Der parallele Zwischenmechanismus besteht aus einem proximalen und distalen Glied. Die proximale Verbindung wird über ein Aluminiumrohr und die distale Komponente über ein Doppelgelenklager realisiert.\\
    \\
    Die Parameter des Delta-Roboters sollen sich an in der Industrie eingesetzten Robotern orientieren. Um folglich eine angemessene Auswahl treffen zu können sind in Tabelle \ref{tab1} die Dimensionen dreier in der Industrie etablierter Delta-Roboter gegenübergestellt.

    \begin{table}[!htbp]
        \centering
        \caption{Dimensionen etalblierter Delta-Roboter \citefigm{SoVa18}{146}}\label{tab1}
            \begin{tabular}{| l | c | c | c |}\hline \rowcolor[gray]{0.8}
                Beschreibung & Proximal Glied [mm] & Distal Glied [mm]  & Proportion\\\hline
                Adept Quattro s650H & 373 & 825 & 2,21\\\hline
                ABB FlexPicker IRB 360-1/1600 & 524 & 1244 & 2,37\\\hline
                FANUC M-1iA/0.5S &  100 & 270 & 2,7\\\hline
            \end{tabular}
    \end{table}
    
     \begin{table}[!htbp]
        \centering
        \caption{Stückliste: Lagernde Teile}\label{tab2}
            
            \begin{tabular}{| l | c |}\hline \rowcolor[gray]{0.8}
                Beschreibung & Verfügbarkeit\\\hline
                
                Hebi X5-1 Motoren & 3/3\\\hline
                Gewindestange M5 600[mm] & 1/1\\\hline
                Aluprofile & 12/12\\\hline
                Aluwinkel & 16/16\\\hline
                Aluwinkelshrauben & 32/32\\\hline
                Nutmuttern 6 M4 & 32/32\\\hline
                M5 x 10 Zylinderkopfschrauben & 36/36\\\hline
                M5 x 16 Zylinderkopfschrauben & 36/36\\\hline
                M4 x 16 Zylinderkopfschrauben & 9/9\\\hline
                M3 x 10 Zylinderkopfschrauben & 3/3\\\hline
                M5 Muttern & 72/72\\\hline
                M5 Hutmuttern & 12/12\\\hline
                M3 Muttern & 3/3\\\hline
                \end{tabular}
    \end{table}
    
    \begin{table}[!htbp]
        \centering
        \caption{Stückliste: Selbst konstruierte Teile SLS}\label{tab3}
            \begin{tabular}{| l | c |}\hline \rowcolor[gray]{0.8}
                Beschreibung & Verfügbarkeit\\\hline
                
                Verbindungszapfen & 6/6\\\hline
                Drehgelenksverbindung & 3/3\\\hline
                Flansch & 1/1\\\hline
                Kalibrierungspin & 1/1\\\hline
                Gelenksgegenstück & 3/6\\\hline
                Basisverbindung & 0/3\\\hline
                Basisverbindunggegenstück & 0/3\\\hline
                Basishalterung & 0/3\\\hline
            \end{tabular}
    \end{table}
    
    \begin{table}[!htbp]
        \centering
        \caption{Stückliste: Zu bestellende Teile}\label{tab4}
            \begin{tabular}{| l | c |}\hline\rowcolor[gray]{0.8}
                Beschreibung & Verfügbarkeit\\\hline
                
                Doppelgelenklager & 0/6\\\hline
                Aluminiumrohr 100[mm] & 0/3\\\hline
                Aluminiumrohr 137.5[mm] & 0/3\\\hline
                Netzteil & 0/1\\\hline
            \end{tabular}
    \end{table}

\section{Entwicklung der Software}
\chapter{Konzeptrealisierung}
    
%     \includemedia[
%      width=0.8\linewidth,height=0.8\linewidth,
%   activate=pageopen,
%   add3Djscript=asylabels.js,
%   add3Djscript=3Dspintool.js,
%   3Dmenu,
%   3Dc2c=1 1 0.2, %object-to-camera vector
%   %settings below found by right-click-->Generate Default View
%   3Dcoo=-1.2360605001449585 -2.1437549591064453 -345.6598815917969,
%   3Droo=377.89275461201964,
%   3Dlights=Headlamp,
%   ]{\includegraphics{delta.PDF}}{delta.prc}

\chapter{Systemtests}
\chapter{Ergebnisse}
\chapter{Evaluierung und Diskussion}
\chapter{Zusammenfassung und Ausblick}

% --------------------------------------------------
% BIBLIOGRAPHY
% --------------------------------------------------
\clearpage
\ifthenelse{\equal{\FHTWCitationType}{HARVARD}}{}{\bibliographystyle{gerabbrv}}
\bibliography{References}
\clearpage

% --------------------------------------------------
% GLOSSARIES
% --------------------------------------------------
% Das Abbildungsverzeichnis
% \listoffigures
% \clearpage

% Das Tabellenverzeichnis
\listoftables
\clearpage

% Das Quellcodeverzeichnis
% \listofcode
% \clearpage

\phantomsection
\addcontentsline{toc}{chapter}{\listacroname}
\chapter*{\listacroname}
\begin{acronym}[XXXXX]
    \acro{DoF}[DoF]{Degree of freedom/Freiheitsgrad}
    \acro{IoT}[IoT]{Internet of things/Internet der Dinge}
    
\end{acronym}

% --------------------------------------------------
% APPENDIX
% --------------------------------------------------
% \clearpage
% \appendix
% \chapter{Anhang A}
% \clearpage
% \chapter{Anhang B}

\end{document}

%%%%%%%%%%%%%%%%%%%%%%%%%%%%%%%%%%%%%%%%%%%%%%%%%%%%
%%                     FIN                        %%
%%%%%%%%%%%%%%%%%%%%%%%%%%%%%%%%%%%%%%%%%%%%%%%%%%%%

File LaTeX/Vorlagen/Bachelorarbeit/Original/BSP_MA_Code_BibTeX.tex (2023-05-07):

%
% FH Technikum Wien
% !TEX encoding = UTF-8 Unicode
%
% Erstellung von Master- und Bachelorarbeiten an der FH Technikum Wien mit Hilfe von LaTeX und der Klasse TWBOOK
%
% Um ein eigenes Dokument zu erstellen, müssen Sie folgendes ergänzen:
% 1) Mit \documentclass[..] einstellen: Master- oder Bachelorarbeit, Studiengang und Sprache
% 2) Mit \newcommand{\FHTWCitationType}.. Zitierstandard festlegen (wird in der Regel vom Studiengang vorgegeben - bitte erfragen)
% 3) Deckblatt, Kurzfassung, etc. ausfüllen
% 4) und die Arbeit schreiben (die verwendeten Literaturquellen in Literatur.bib eintragen)
%
% Getestet mit TeXstudio mit Zeichenkodierung ISO-8859-1 (=ansinew/latin1) und MikTex unter Windows
% Zu beachten ist, dass die Kodierung der Datei mit der Kodierung des paketes inputenc zusammen passt!
% Die Kodierung der Datei twbook.cls MUSS ANSI betragen!
% Bei der Verwendung von UTF8 muss dnicht nur die Kodierung des Dokuments auf UTF8 gestellt sein, sondern auch die des BibTex-Files!
%
% Bugreports und Feedback bitte per E-Mail an latex@technikum-wien.at
%
% Versionen
% *) V0.7: 9.1.2015, RO: Modeline angepasst und verschoben
% *) V0.6: 10.10.2014, RO: Weitere Anpassung an die UK
% *) V0.5: 8.8.2014, WK: Literaturquellen überarbeitet und angepasst
% *) V0.4: 4.8.2014, WK: Initalversion in SVN eingespielt
%
\documentclass[MMR,Master,english]{twbook}%\documentclass[Bachelor,BMR,ngerman]{twbook}
\usepackage[utf8]{inputenc}
\usepackage[T1]{fontenc}

%
% Bitte in der folgenden Zeile den Zitierstandard festlegen
\newcommand{\FHTWCitationType}{HARVARD} % IEEE oder HARVARD möglich - wenn Sie zwischen IEEE und HARVARD wechseln, bitte die temorären Dateien (aux, bbl, ...) löschen
%
\ifthenelse{\equal{\FHTWCitationType}{HARVARD}}{\usepackage{harvard}}{\usepackage{bibgerm}}

% Definition Code-Listings Formatierung:
\usepackage[final]{listings}
\lstset{captionpos=b, numberbychapter=false,caption=\lstname,frame=single, numbers=left, stepnumber=1, numbersep=2pt, xleftmargin=15pt, framexleftmargin=15pt, numberstyle=\tiny, tabsize=3, columns=fixed, basicstyle={\fontfamily{pcr}\selectfont\footnotesize}, keywordstyle=\bfseries, commentstyle={\color[gray]{0.33}\itshape}, stringstyle=\color[gray]{0.25}, breaklines, breakatwhitespace, breakautoindent}
\lstloadlanguages{[ANSI]C, C++, [gnu]make, gnuplot, Matlab}

%Formatieren des Quellcodeverzeichnisses
\makeatletter
% Setzen der Bezeichnungen für das Quellcodeverzeichnis/Abkürzungsverzeichnis in Abhängigkeit von der eingestellten Sprache
\providecommand\listacroname{}
\@ifclasswith{twbook}{english}
{%
    \renewcommand\lstlistingname{Code}
    \renewcommand\lstlistlistingname{List of Code}
    \renewcommand\listacroname{List of Abbreviations}
}{%
    \renewcommand\lstlistingname{Quellcode}
    \renewcommand\lstlistlistingname{Quellcodeverzeichnis}
    \renewcommand\listacroname{Abkürzungsverzeichnis}
}
% Wenn die Option listof=entryprefix gewählt wurde, Definition des Entyprefixes für das Quellcodeverzeichnis. Definition des Macros listoflolentryname analog zu listoflofentryname und listoflotentryname der KOMA-Klasse
\@ifclasswith{scrbook}{listof=entryprefix}
{%
    \newcommand\listoflolentryname\lstlistingname
}{%
}
\makeatother
\newcommand{\listofcode}{\phantomsection\lstlistoflistings}

% Die nachfolgenden Pakete stellen sonst nicht benötigte Features zur Verfügung
\usepackage{blindtext}

%
% Einträge für Deckblatt, Kurzfassung, etc.
%
\title{Arbeitstitel\\Arbeitstitel}
\author{Titel Vorname Name, Titel}
\studentnumber{XXXXXXXXXXXXXXX}
%\author{Titel Vorname Name, Titel\and{}Titel Vorname Name, Titel}
%\studentnumber{XXXXXXXXXXXXXXX\and{}XXXXXXXXXXXXXXX}
\supervisor{Titel Vorname Name, Titel}
%\supervisor[Begutachter]{Titel Vorname Name, Titel}
%\supervisor[Begutachterin]{Titel Vorname Name, Titel}
%\secondsupervisor{Titel Vorname Name, Titel}
%\secondsupervisor[Begutachter]{Titel Vorname Name, Titel}
%\secondsupervisor[Begutachterinnen]{Titel Vorname Name, Titel}
\place{Wien}
\kurzfassung{\blindtext}
\schlagworte{Schlagwort1, Schlagwort2, Schlagwort3, Schlagwort4}
\outline{\blindtext}
\keywords{Keyword1, Keyword2, Keyword3, Keyword4}
%\acknowledgements{\blindtext}

\begin{document}

%Festlegungen für den HARVARD-Zitierstandard
\ifthenelse{\equal{\FHTWCitationType}{HARVARD}}{
\bibliographystyle{Harvard_FHTW_MR}%Zitierstandard FH Technikum Wien, Studiengang Mechatronik/Robotik, Version 1.2e
\citationstyle{dcu}%Correct citation-style (Harvardand, ";" between citations, "," between author and year)
\citationmode{abbr}%use "et al." with first citation
\iflanguage{ngerman}{
    %Deutsch Neue Rechtschreibung
    \newcommand{\citepic}[1]{(Quelle: \protect\cite{#1})}%Zitat: Bild
    \newcommand{\citefig}[2]{(Quelle: \protect\cite{#1}, S. #2)}%Zitat: Bild aus Dokument
    \newcommand{\citefigm}[2]{(Quelle: modifiziert "ubernommen aus \protect\cite{#1}, S. #2)}%Zitat: modifiziertes Bild aus Dokument
    \newcommand{\citep}{\citeasnoun}%In-Line Zitiat entweder mit \citep{} oder \citeasnoun{}
    \newcommand{\acessedthrough}{Verf{\"u}gbar unter:}%Für URL-Angabe
    \newcommand{\acessedthroughp}{Verf{\"u}gbar bei:}%Für URL-Angabe (Geschützte Datenbank, Zugriff durch FH)
    \newcommand{\acessedat}{Zugang am}%Für URL-Datum-Angabe
    \newcommand{\singlepage}{S.}%Für Seitenangabe (einzelne Seite)
    \newcommand{\multiplepages}{S.}%Für Seitenangabe (mehrere Seiten)
    \newcommand{\chapternr}{K.}%Für Kapitelangabe
    \renewcommand{\harvardand}{\&}%Harvardand in Zitaten
    \newcommand{\abstractonly}{ausschließlich Abstract}
    \newcommand{\edition}{. Auflage}%Angabe der Auflage
}{
\iflanguage{german}{
    %Deutsch
    \newcommand{\citepic}[1]{(Quelle: \protect\cite{#1})}%Zitat: Bild
    \newcommand{\citefig}[2]{(Quelle: \protect\cite{#1}, S. #2)}%Zitat: Bild aus Dokument
    \newcommand{\citefigm}[2]{(Quelle: modifiziert "ubernommen aus \protect\cite{#1}, S. #2)}%Zitat: modifiziertes Bild aus Dokument
    \newcommand{\citep}{\citeasnoun}%In-Line Zitiat entweder mit \citep{} oder \citeasnoun{}
    \newcommand{\acessedthrough}{Verf{\"u}gbar unter:}%Für URL-Angabe
    \newcommand{\acessedthroughp}{Verf{\"u}gbar bei:}%Für URL-Angabe (Geschützte Datenbank, Zugriff durch FH)
    \newcommand{\acessedat}{Zugang am}%Für URL-Datum-Angabe
    \newcommand{\singlepage}{S.}%Für Seitenangabe (einzelne Seite)
    \newcommand{\multiplepages}{S.}%Für Seitenangabe (mehrere Seiten)
    \newcommand{\chapternr}{K.}%Für Kapitelangabe
    \renewcommand{\harvardand}{\&}%Harvardand in Zitaten
    \newcommand{\abstractonly}{ausschließlich Abstract}
    \newcommand{\edition}{. Auflage}%Angabe der Auflage
}{
    %Englisch
    \newcommand{\citepic}[1]{(Source: \protect\cite{#1})}%Zitat: Bild
    \newcommand{\citefig}[2]{(Source: \protect\cite{#1}, p. #2)}%Zitat: Bild aus Dokument
    \newcommand{\citefigm}[2]{(Source: taken with modification from \protect\cite{#1}, p. #2)}%Zitat: modifiziertes Bild aus Dokument
    \newcommand{\citep}{\citeasnoun}%In-Line Zitiat entweder mit \citep{} oder \citeasnoun{}
    \newcommand{\acessedthrough}{Available at:}%Für URL-Angabe
    \newcommand{\acessedthroughp}{Available through:}%Für URL-Angabe (Geschützte Datenbank, Zugriff durch FH)
    \newcommand{\acessedat}{Accessed}%Für URL-Datum-Angabe
    \newcommand{\singlepage}{p.}%Für Seitenangabe (einzelne Seite)
    \newcommand{\multiplepages}{pp.}%Für Seitenangabe (mehrere Seiten)
    \newcommand{\chapternr}{Ch.}%Für Kapitelangabe
    \renewcommand{\harvardand}{\&}%Harvardand in Zitaten
    \newcommand{\abstractonly}{Abstract only}
    \newcommand{\edition}{~edition}%Edition -> note, that you have to write "edition = {2nd},"!
}}}

\maketitle

%
% .. und hier beginnt die eigentliche Arbeit. Viel Erfolg beim Verfassen!
%
\chapter{Erste Überschrift der Ebene 1 (chapter)}
\blinddocument

\blindmathpaper

\section{Erste Überschrift Tiefe 2 (section)}
\blindtext

\subsection{Erste Überschrift Tiefe 3 (subsection)}
\blindtext

\subsubsection{Erste Überschrift Tiefe 4 (subsubsection)}
\blindtext

\chapter{Zweite Überschrift der Tiefe 1 (chapter)}
\blindtext

\section{Zweite Überschrift Tiefe 2 (section)}
\blindtext

\section{Zweite Überschrift Tiefe 2 (section)}
\blindtext

\subsection{Zweite Überschrift Tiefe 3 (subsection)}
\blindtext

\subsection{Dritte Überschrift Tiefe 3 (subsection)}
\blindtext

\subsubsection{Zweite Überschrift Tiefe 4 (subsubsection)}
\blindtext

\noindent Querverweise werden in \LaTeX{} automatisch erzeugt und verwaltet, damit sie leicht aktualisiert werden können. Hier wird zum Beispiel auf Abbildung \ref{Abb1} verwiesen.

\begin{figure}[!htbp]
\centering

\caption{Beispiel für die Beschriftung eines Buchrückens.}\label{Abb1}
\end{figure}
\begin{figure}[!htbp]
\centering

\caption{2. Beispiel für die Beschriftung eines Buchrückens.}\label{Abb2}
\end{figure}

Und hier ist ein Verweis auf Tabelle \ref{tab1}. Das gezeigte Tabellenformat ist nur ein Beispiel. Tabellen können individuell gestaltet werden.

\begin{table}[!htbp]
\centering
\caption{Semesterplan der Lehrveranstaltung \glqq Angewandte Mathematik\grqq.}\label{tab1}
\begin{tabular}{| p{0.3\linewidth} | p{0.3\linewidth} | p{0.3\linewidth} |}\hline
Datum & Thema & Raum\\\hline
20.08.2008 & Graphentheorie & HS 3.13\\
01.10.2008 & Biomathematik & HS 1.05\\\hline
\end{tabular}
\end{table}
\begin{table}[!htbp]
\centering
\caption{2. Semesterplan der Lehrveranstaltung \glqq Angewandte Mathematik\grqq.}\label{tab2}
\begin{tabular}{| p{0.3\linewidth} | p{0.3\linewidth} | p{0.3\linewidth} |}\hline
Datum & Thema & Raum\\\hline
20.08.2008 & Graphentheorie & HS 3.13\\
01.10.2008 & Biomathematik & HS 1.05\\\hline
\end{tabular}
\end{table}

Hier wird auf die Formel \ref{Gl1} verwiesen.

\begin{align}
x = -\frac{p}{2}\pm\sqrt{\frac{p^2}{4}-q}\label{Gl1}
\end{align}
\begin{align}
x = -\frac{p}{2}\pm\sqrt{\frac{p^2}{4}-q}\label{Gl2}
\end{align}

\begin{lstlisting}[language=C++,name={1. Beispiel},label={sc:bsp:1}]
#include <iostream>

void SayHello(void)
{
    // Kommentar
    cout << "Hello World!" << endl;
}

int main(int argc, char **argv)
{
    SayHello();
    return 0;
}
\end{lstlisting}

Literaturverweise sollten automatisch verwaltet werden, vor allem, wenn es viele Quellenverweise gibt. Beispiele sind  \cite{Ko05a}, \cite{Ko05b}, \cite{MiGo05}, \cite{TeGo14}, \cite{HuHa07}, \cite{HuZi10}, \cite{ZiKu07}, \cite{He07}, \cite{SIE11}, \cite{SIE14}, \cite{ISO98}, \cite{ATM11}, \cite{Hu11}, \cite{Po10}. Das verwendete Zitierformat (bzw.~das Format des Literaturverzeichnisses) ist entspechend der Vorgaben der Studiengänge zu wählen.
Es wird dringend empfohlen, BibTeX~zu verwenden (wie in diesem Beispiel).
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

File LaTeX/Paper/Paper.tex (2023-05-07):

%%%%%%%%%%%%%%%%%%%%%%%%%%%%%%%%%%%%%%%%%%%%%%%%%%%%%%%%%%%%%%%%%%%%%%%%%%
% ------------------------------------------------------------------------
% LaTeX FHPaper Template by Thomas MIGLINCI
% ------------------------------------------------------------------------
%
% Das eigentliche Paper beginnt ab Zeile 124 - dort die Daten in den
% Aufruf von FHInfo eintragen.
%
% Bitte ersetzen Sie gegebenenfalls Master-Studiengang Mechatronik/Robotik durch Bachelor-.....
%
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

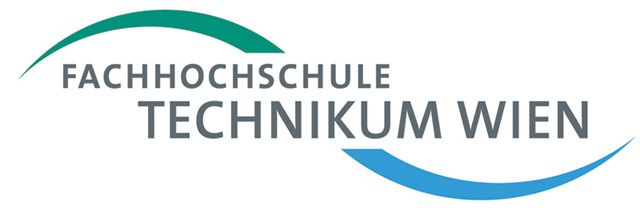
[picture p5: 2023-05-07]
LaTeX/Paper/fh_welle.jpg

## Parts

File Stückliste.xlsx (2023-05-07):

Kategorie | Produkt | Beschreibung | Anzahl (benötigt) | Anzahl (bestellen) | Preis/Stk. [€] | Versandkosten | Preis [€]
Hebi | X5-1 | Motoren | 3 | - | - | - | #VALUE!
Hebi | Output Tube Adapter | A-2038-02: X-Series 1.25" Tube Adapter with Indexing Pin (Output) | 3 | - | - | - | 0
Hebi | T-Slot Mounting Plate (modifiziert) | A-2043-01: X-Series T-Slot Mounting Plate (1" or 25mm) | 3 | - | - | - | 0
Hebi | Aufnahmestern mit Anschlussbohrungen für Zubehör | ETY-DR-0009 | 1 | - | - | - | #VALUE!
Hebi | Verbindungsteil zwischen Aufnahmestern und Doppelgelenklager | ETY-DR-0012 | 12 | - | - | - | #VALUE!
Igus | Robolink® W Anschlussrohr aus Aluminium | Durchmesser: 26 [mm] - Länge: 150 [mm], https://www.igus.at/product/1416 | 3 | 3 | 6.3 |  | 18.9
Igus | Igubal®-Doppelgelenklager KDGM | KDGM-10-A-ER-J (Version A), Durchmesser: 10 [mm] - Länge: 380 [mm], https://www.igus.at/info/spherical-bearings-double-spherical-kdgm | 6 | 6 | Auf Anfrage |  | Auf Anfrage
Accessory | Power Supply | MEAN WELL GST220A24-R7B, https://www.conrad.at/de/tischnetzteil-festspannung-mean-well-gst220a24-r7b-24-vdc-92-a-220-w-1439256.html | 1 | 1 | 179 | 0 | 179
Accessory | Gewindestange M5 | 1.000 [mm] Edelstahl, https://www.obi.at/gewindestangen/lux-gewindestangen-m5-x-1-000-mm-edelstahl/p/7608813 | 1 | 1 | 3.29 | 2.99 | 6.28
Accessory | Aluprofile | 20 [mm] - Länge: 400 [mm] | 6 | 0 | 0 | - | 0
Accessory | Aluprofile | 20 [mm] - Länge: 600 [mm] | 3 | 0 | 0 | - | 0
 | Bereits vorhanden
 | Konstruieren (abgeschlossen)
 | Bestellen
 | Konstruieren (ausständig)
 | Bestellseiten: robotunits, igus

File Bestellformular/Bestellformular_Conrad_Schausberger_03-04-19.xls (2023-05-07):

Bestellformular
 |  |  |  |  |  | Datum: | 2019-04-03
Name: | Felix Schausberger
Projektgruppe: |  | 7
Betreuer: | Mohamed Aburaia, MSc
Unterschrift des Fachbetreuers (Genehmigung) |  |  |  | Unterschrift des Projektkoordinators (Genehmigung)
Firma: | Name d. Firma: |  | Conrad Electronic GmbH & Co KG
 | Adresse: |  | Durisolstraße 2, 4600 Wels
 | Homepage: |  | https://www.conrad.at/
 | Ansprechpartner: |  | sales@conrad.at
Pos | Menge | VE | Bezeichnung | Artikelnr. | Preis/VE (Netto) | Preis/VE (Brutto) | Preis/GE (Brutto) | Ust [%]
1. | 1 | 1 | Mean Well GST220A24-R7B | 4021087028783 | 149.17 | 179.00 | 179.00 | 20
2. |  |  |  |  | 0.00 | 0.00 | 0.00 | 20
3. |  |  |  |  | 0.00 | 0.00 | 0.00 | 20
4. |  |  |  |  | 0.00 | 0.00 | 0.00 | 20
5. |  |  |  |  | 0.00 | 0.00 | 0.00 | 20
 |  |  |  |  |  | Summe Brutto: | 179.00
 |  |  |  |  |  | Versandkosten: | 0.00
 |  |  |  |  |  | Gesamt | 179.00 €
Alle hellgrau unterlegten Felder sind auszufüllen!
Sollte sich die Bestellung auf ein Angebot oder einen Kostenvoranschlag beziehen, sind diese beizufügen.

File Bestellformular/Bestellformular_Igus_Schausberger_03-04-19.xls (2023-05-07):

Bestellformular
 |  |  |  |  |  | Datum: | 2019-04-03
Name: | Felix Schausberger
Projektgruppe: |  | 7
Betreuer: | Mohamed Aburaia, MSc
Unterschrift des Fachbetreuers (Genehmigung) |  |  |  | Unterschrift des Projektkoordinators (Genehmigung)
Firma: | Name d. Firma: |  | igus® GmbH
 | Adresse: |  | Spicher Straße 1a, D-51147 Köln
 | Homepage: |  | https://www.igus.at/
 | Ansprechpartner: |  | Herr Oliver Plasch, +43 7662 57763
Pos | Menge | VE | Bezeichnung | Artikelnr. | Preis/VE (Netto) | Preis/VE (Brutto) | Preis/GE (Brutto) | Ust [%]
1. | 6 | 1 | igubal®-Doppelgelenklager KDGM | KDGM-10-A-ER-J | 7.95 | 9.54 | 57.24 | 20
2. | 3 | 1 | robolink® W Anschlussrohr aus Aluminium, 137.5 mm | RL-TAL-26 | 4.82 | 5.78 | 17.35 | 20
3. |  |  |  |  | 0.00 | 0.00 | 0.00 | 20
4. |  |  |  |  | 0.00 | 0.00 | 0.00 | 20
5. |  |  |  |  | 0.00 | 0.00 | 0.00 | 20
 |  |  |  |  |  | Summe Brutto: | 74.59
 |  |  |  |  |  | Versandkosten: | 0.00
 |  |  |  |  |  | Gesamt | 74.59 €
Alle hellgrau unterlegten Felder sind auszufüllen!
Sollte sich die Bestellung auf ein Angebot oder einen Kostenvoranschlag beziehen, sind diese beizufügen.

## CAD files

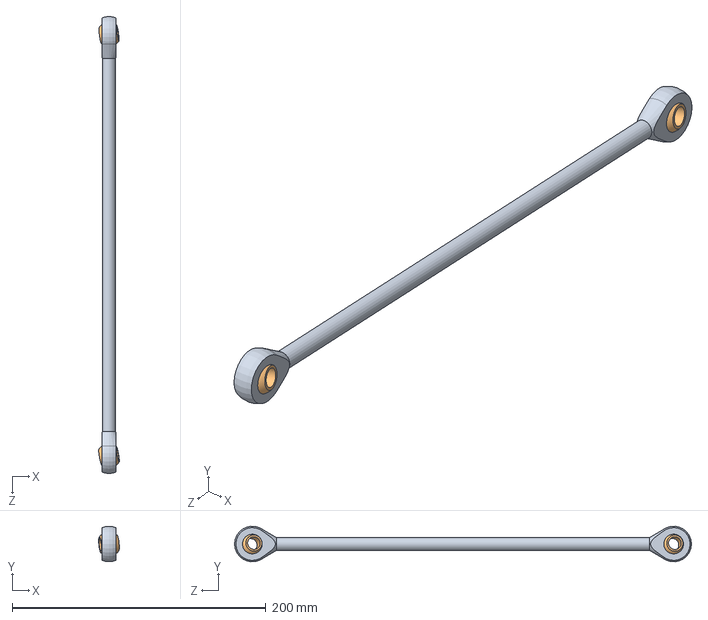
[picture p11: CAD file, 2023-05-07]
CAD/Accessory/distal-link/distal-link.SLDASM
16.3 x 28.0 x 360.1 mm
distal-link-housing
distal-link-sphere x 2

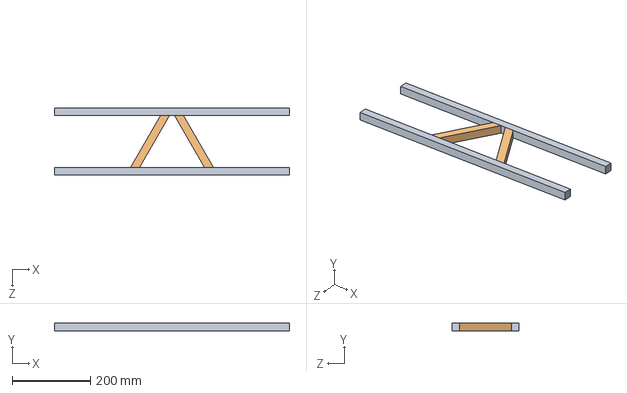
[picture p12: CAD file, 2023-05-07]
CAD/Accessory/frame/Frame test/frame-test.SLDASM
600.0 x 20.0 x 172.2 mm
frame-length x 2
frame-cross-strut x 2

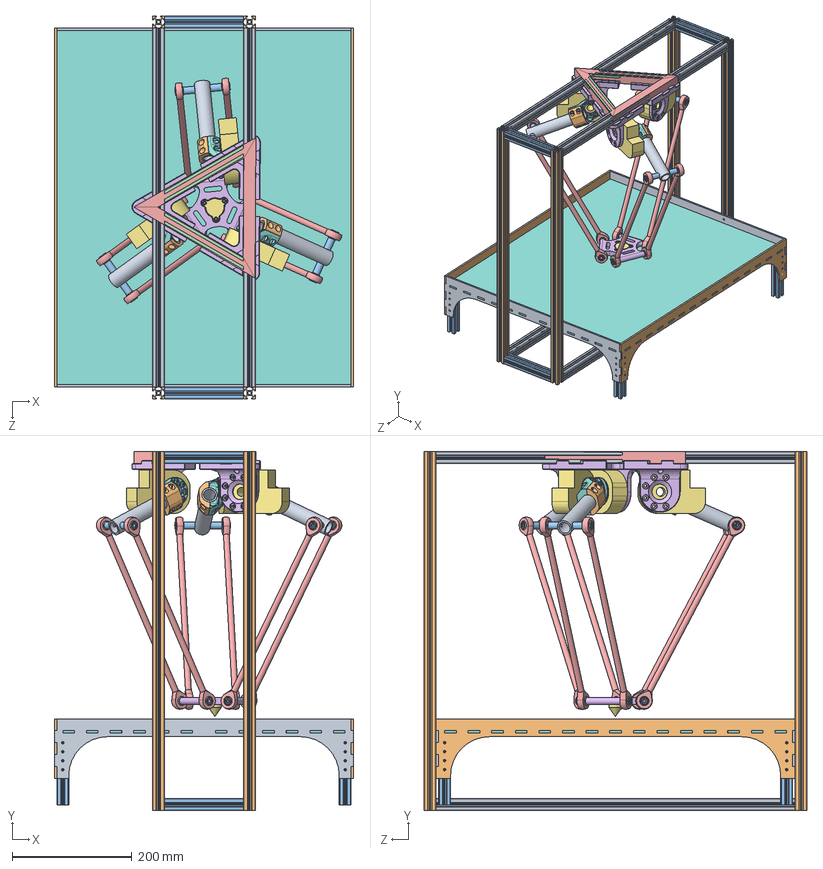
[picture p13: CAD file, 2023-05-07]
CAD/delta-attached-dynamic-with-workspace.SLDASM
500.0 x 600.0 x 640.0 mm
alu-frame-length x 4
alu-frame-height x 4
alu-frame-width x 4
alu-frame-cross-strut x 2
frame-strut-triangle x 3
base-mount x 3
Hebi-X5-1_draft x 3
revolute-joint x 3
proximal-link x 3
joint-clamp x 3
connection-tap-joint x 6
distal-link-sphere x 12
distal-link-housing x 6
flange-star
calibration-pin
basepanel
sidepanel x 2
rearpanel x 2
alu-pillar x 4

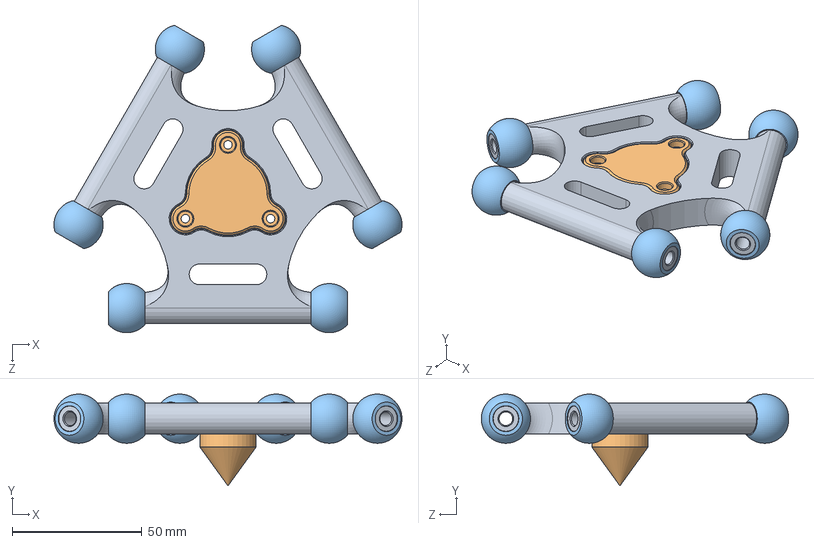
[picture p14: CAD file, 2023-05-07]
CAD/Subassemblies/flange.SLDASM
134.4 x 35.5 x 118.7 mm
flange-star
calibration-pin
distal-link-sphere x 6

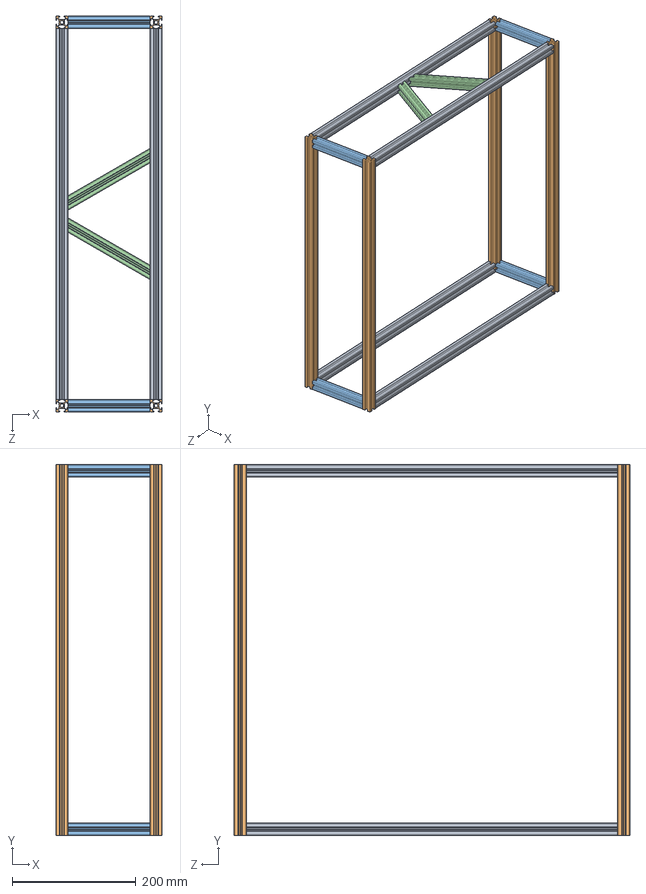
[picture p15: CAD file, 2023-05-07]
CAD/Accessory/frame/frame.SLDASM
172.2 x 600.0 x 640.0 mm
alu-frame-length x 4
alu-frame-height x 4
alu-frame-width x 4
alu-frame-cross-strut x 2

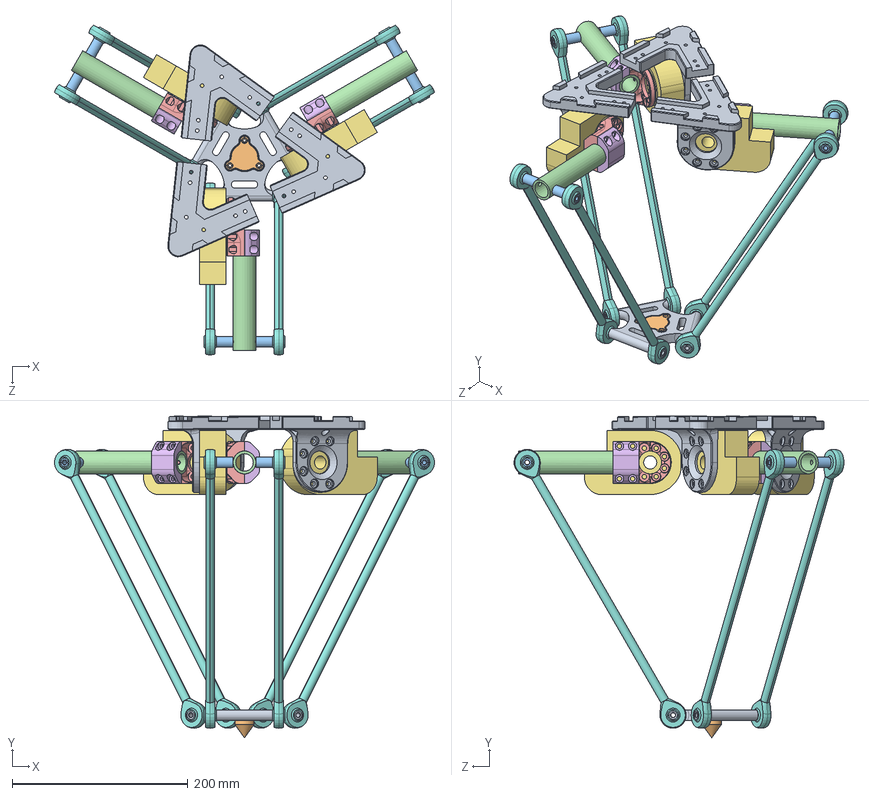
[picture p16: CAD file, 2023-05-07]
CAD/delta-unattached-static.SLDASM
432.5 x 366.2 x 375.5 mm
flange-star
calibration-pin
connection-tap-joint x 6
proximal-link x 3
revolute-joint x 3
joint-clamp x 3
Hebi-X5-1_draft x 3
KDGM_10_A_ER_J_2.stp x 6
base-mount x 3

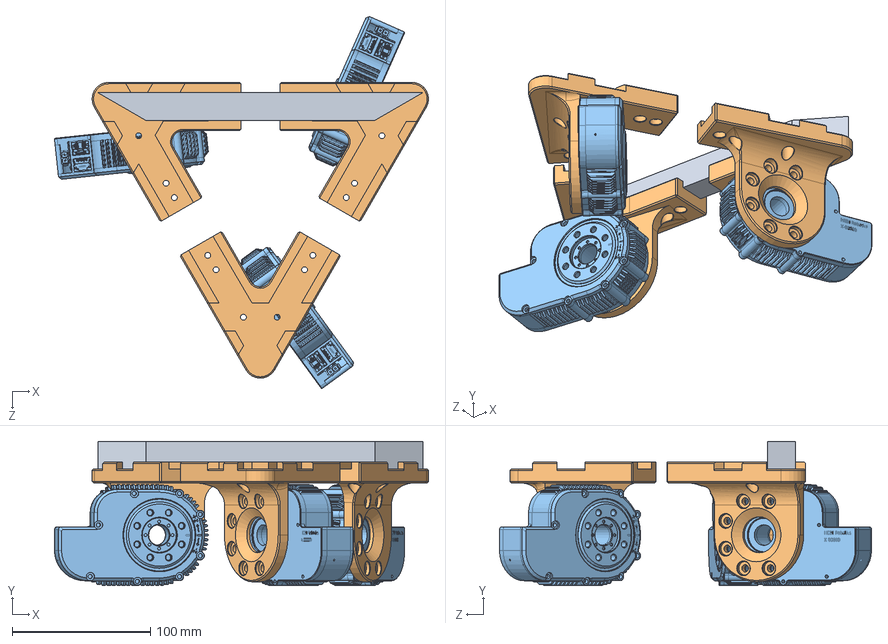
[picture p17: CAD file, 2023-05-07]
CAD/Subassemblies/base-v2.SLDASM
270.4 x 104.2 x 268.8 mm
base-mount x 3
HEBI-X5-1 x 3

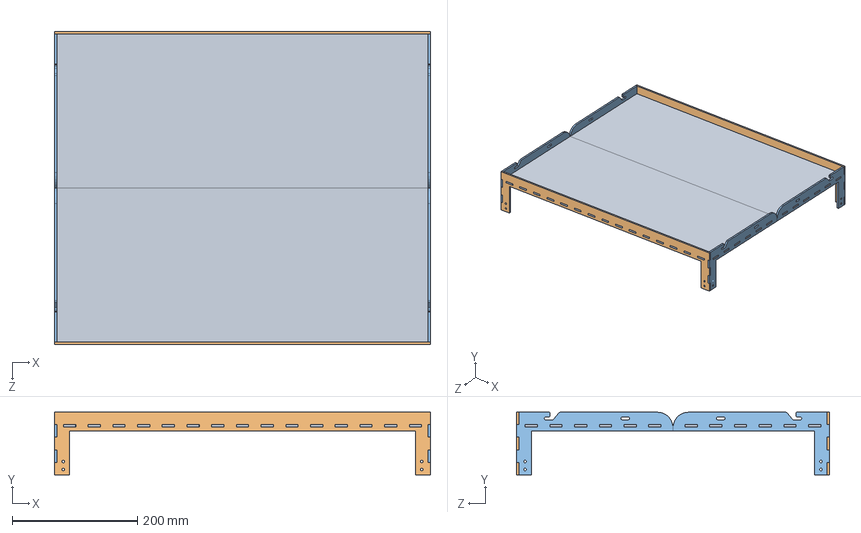
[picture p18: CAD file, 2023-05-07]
CAD/workspace/foldable/workspace.SLDASM
600.0 x 100.0 x 500.0 mm
basepanel x 2
rearpanel x 2
sidepanel x 4

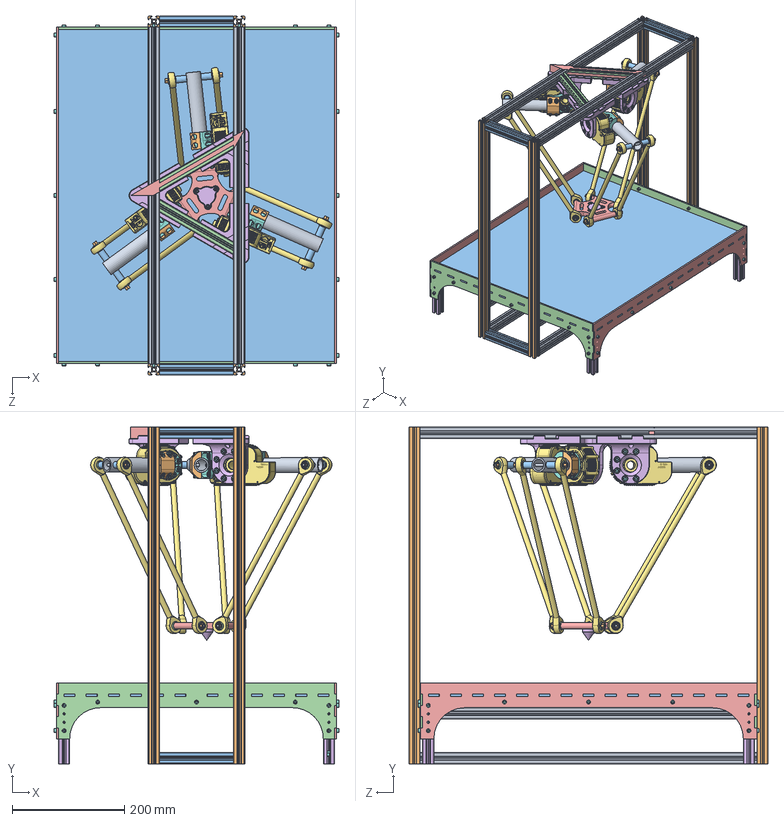
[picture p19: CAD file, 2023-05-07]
CAD/delta-attached-static-v3.SLDASM
508.0 x 600.0 x 640.0 mm
alu-frame-length x 6
alu-frame-height x 4
alu-frame-width x 4
alu-frame-cross-strut x 2
base-mount x 3
HEBI-X5-1 x 3
revolute-joint x 3
proximal-link x 3
joint-clamp x 3
connection-tap-joint x 6
distal-link-sphere x 12
flange-star
calibration-pin
distal-link-housing x 6
socket head cap screw_iso x 109
connection x 6
hex nut gradec_iso x 12
basepanel
sidepanel x 2
rearpanel x 2
alu-pillar x 4
alu-width x 2
alu-length x 2

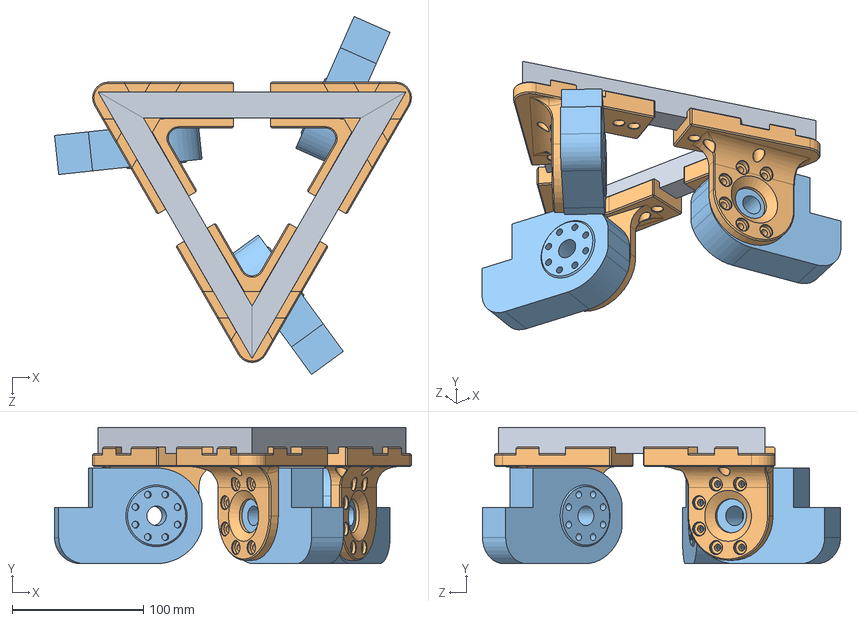
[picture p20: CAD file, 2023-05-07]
CAD/Subassemblies/base.SLDASM
272.3 x 104.0 x 273.1 mm
frame-strut-triangle x 3
base-mount x 3
Hebi-X5-1_draft x 3

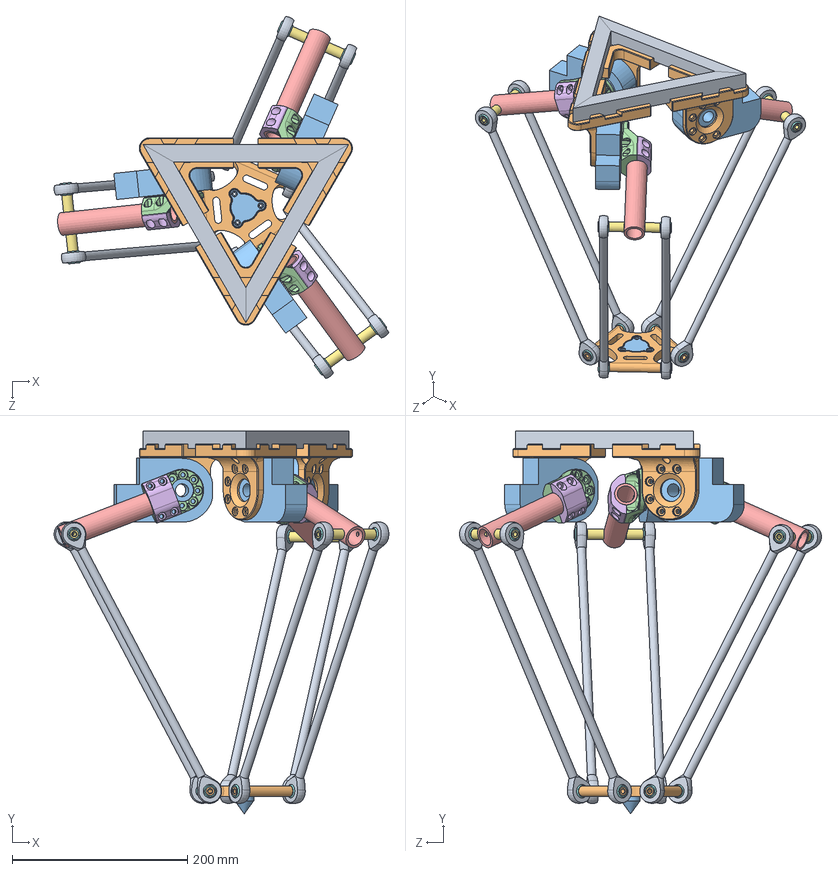
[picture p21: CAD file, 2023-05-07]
CAD/delta-unattached-dynamic.SLDASM
381.9 x 436.8 x 413.0 mm
frame-strut-triangle x 3
base-mount x 3
Hebi-X5-1_draft x 3
revolute-joint x 3
proximal-link x 3
joint-clamp x 3
connection-tap-joint x 6
distal-link-sphere x 12
distal-link-housing x 6
flange-star
calibration-pin

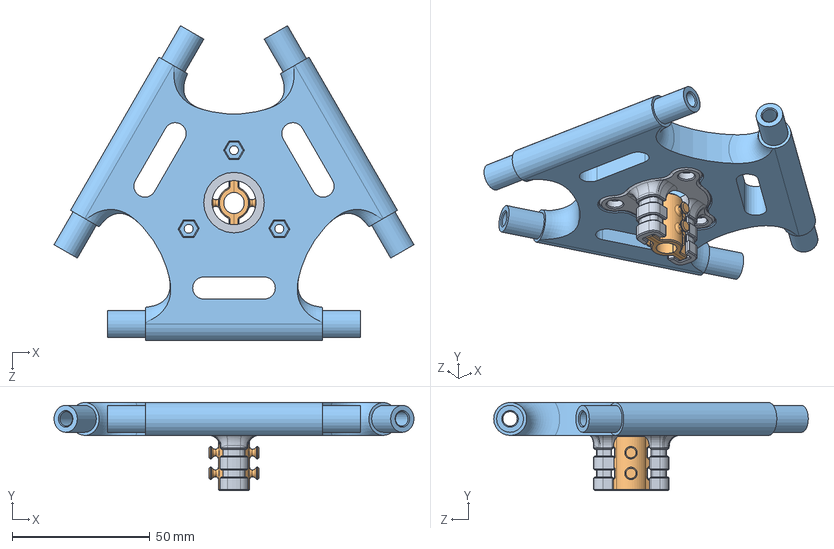
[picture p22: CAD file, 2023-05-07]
CAD/Subassemblies/pen-holder.SLDASM
130.7 x 32.0 x 114.2 mm
pen-holder-duct
pen-holder x 2
flange-star

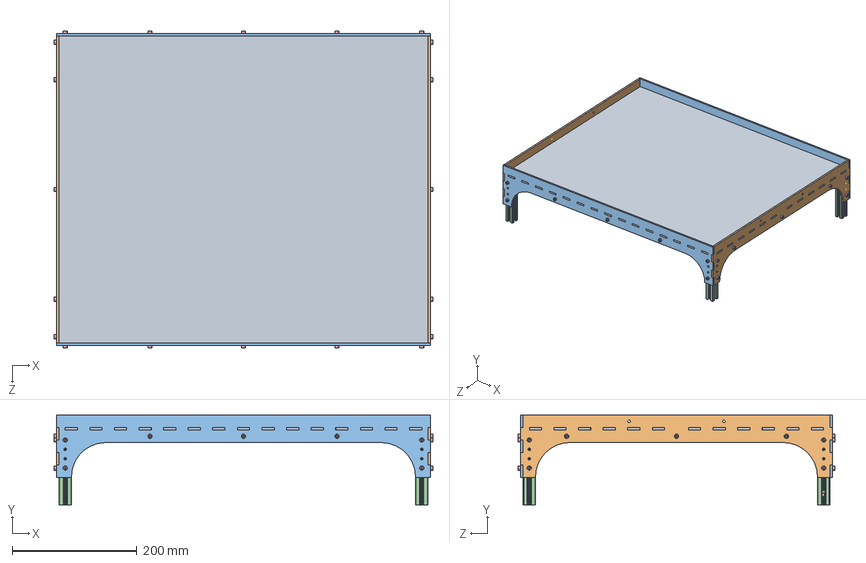
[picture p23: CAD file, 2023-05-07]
CAD/workspace/static/v3/workspace.SLDASM
607.6 x 144.0 x 508.0 mm
basepanel
sidepanel x 2
rearpanel x 2
alu-pillar x 4
socket head cap screw_iso x 29
alu-width x 2
alu-length x 2

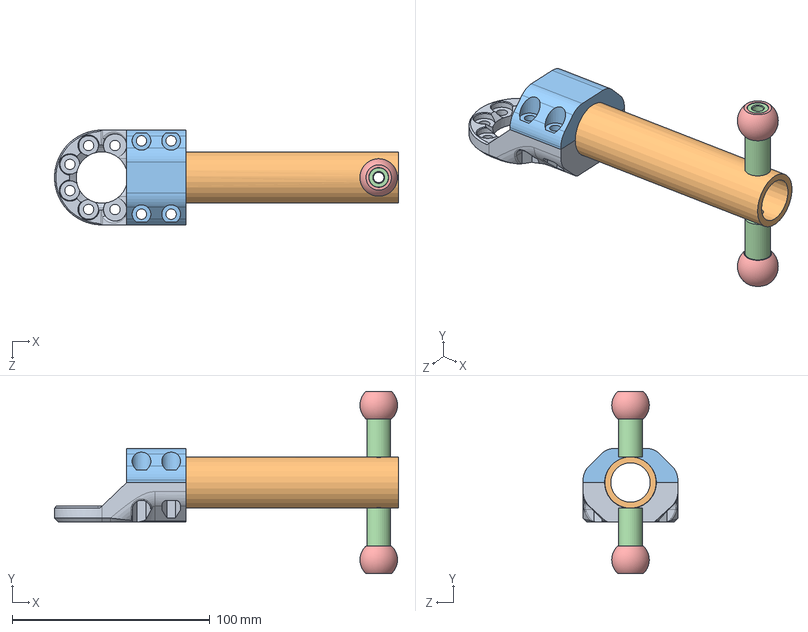
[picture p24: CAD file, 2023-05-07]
CAD/Subassemblies/proximal-link.SLDASM
174.0 x 92.2 x 48.0 mm
revolute-joint
proximal-link
joint-clamp
connection-tap-joint x 2
distal-link-sphere x 2

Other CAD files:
CAD/Accessory/frame/Triangle/frame-triangle.SLDASM
Bestellformular/SLS_Schausberger_18-03-19/SLS_Schausberger_18-03-19/revolute-joint.STL
Bestellformular/SLS_Schausberger_25-03-19/SLS_Schausberger_25-03-19/base_mount.STL
CAD/Accessory/Abdeckkappe_v2.SLDPRT
Bestellformular/SLS_Schausberger_18-03-19/SLS_Schausberger_18-03-19/calibration_pin.STL
Bestellformular/SLS_Schausberger_18-03-19/SLS_Schausberger_18-03-19/connection-tap-joint.STL
Bestellformular/SLS_Schausberger_18-03-19/SLS_Schausberger_18-03-19/flange-star.STL
Bestellformular/SLS_Schausberger_18-03-19/SLS_Schausberger_18-03-19/revolute-joint-clamp.STL
CAD/Accessory/Abdeckkappe.SLDPRT
CAD/Accessory/actuator/HEBI-X5-1.SLDPRT
CAD/Accessory/actuator/HEBI-X5-1_export.STL
CAD/Accessory/actuator/Hebi-X5-1_draft.SLDPRT
CAD/Accessory/connection.SLDPRT
CAD/Accessory/distal-link/distal-link-KDGM-10-A-ER-J.stp
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

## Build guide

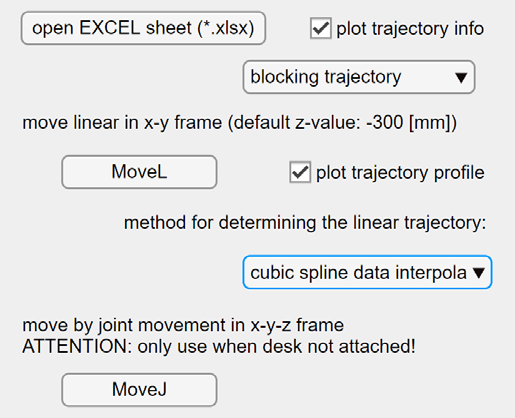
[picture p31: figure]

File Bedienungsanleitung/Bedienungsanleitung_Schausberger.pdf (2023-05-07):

## Bedienungsanleitung für den Delta Roboter

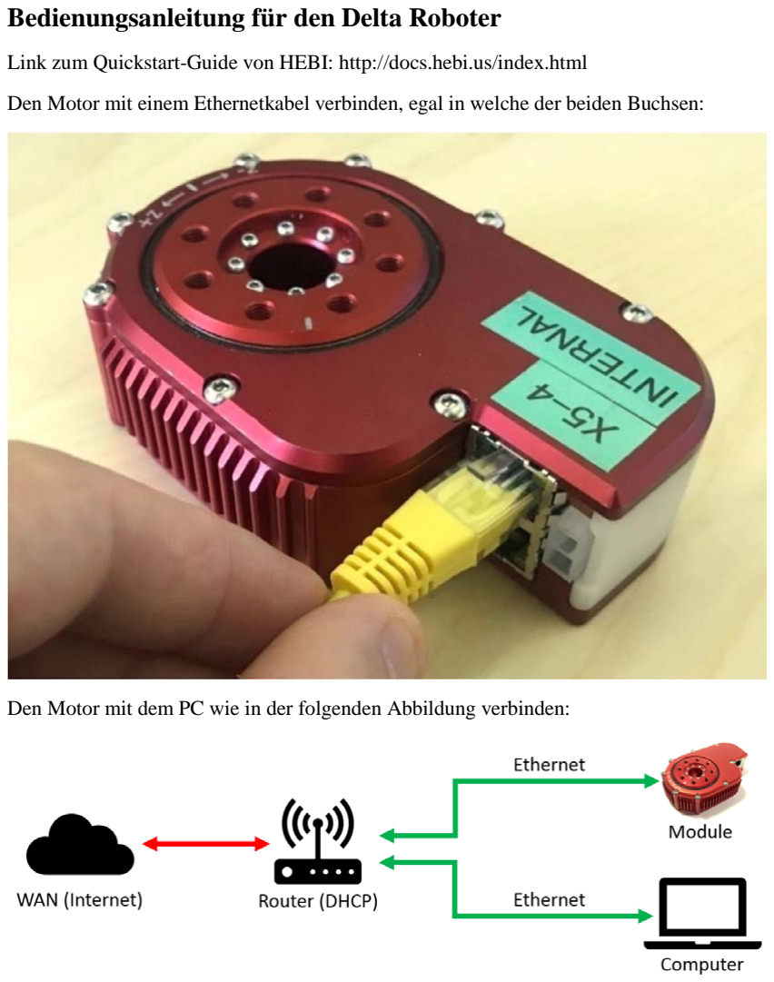
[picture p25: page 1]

Link zum Quickstart-Guide von HEBI: http://docs.hebi.us/index.html
Den Motor mit einem Ethernetkabel verbinden, egal in welche der beiden Buchsen:

Den Motor mit dem PC wie in der folgenden Abbildung verbinden:

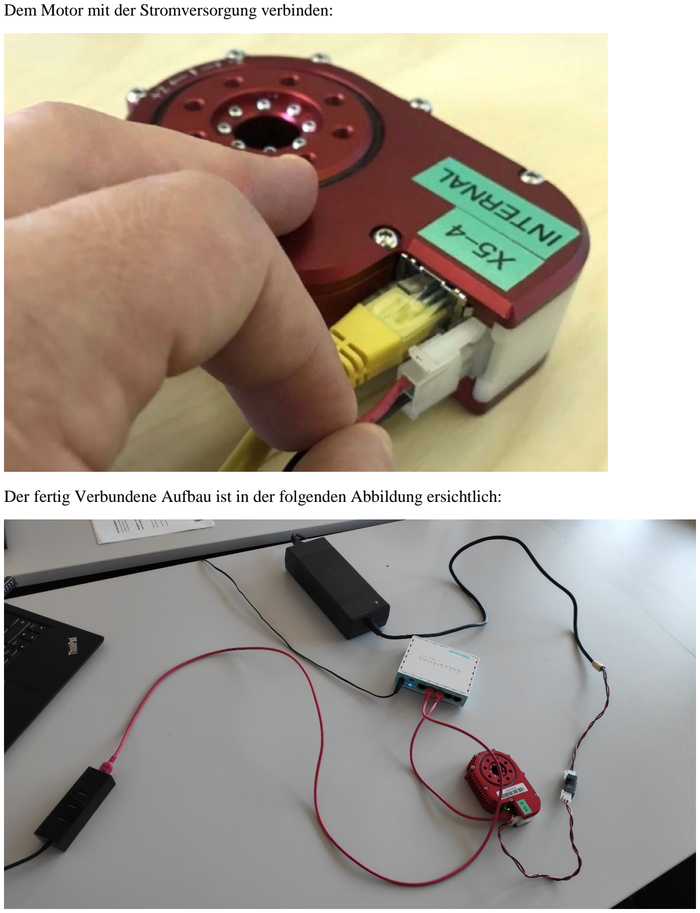
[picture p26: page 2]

Dem Motor mit der Stromversorgung verbinden:

Der fertig Verbundene Aufbau ist in der folgenden Abbildung ersichtlich:

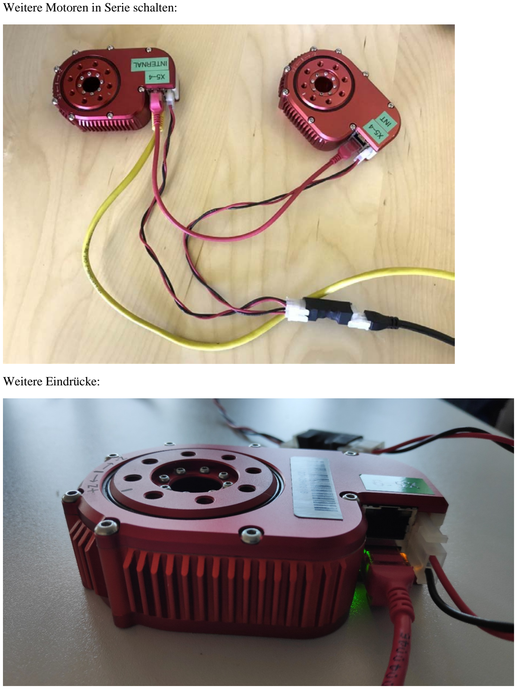
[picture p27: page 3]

Weitere Motoren in Serie schalten:

Weitere Eindrücke:

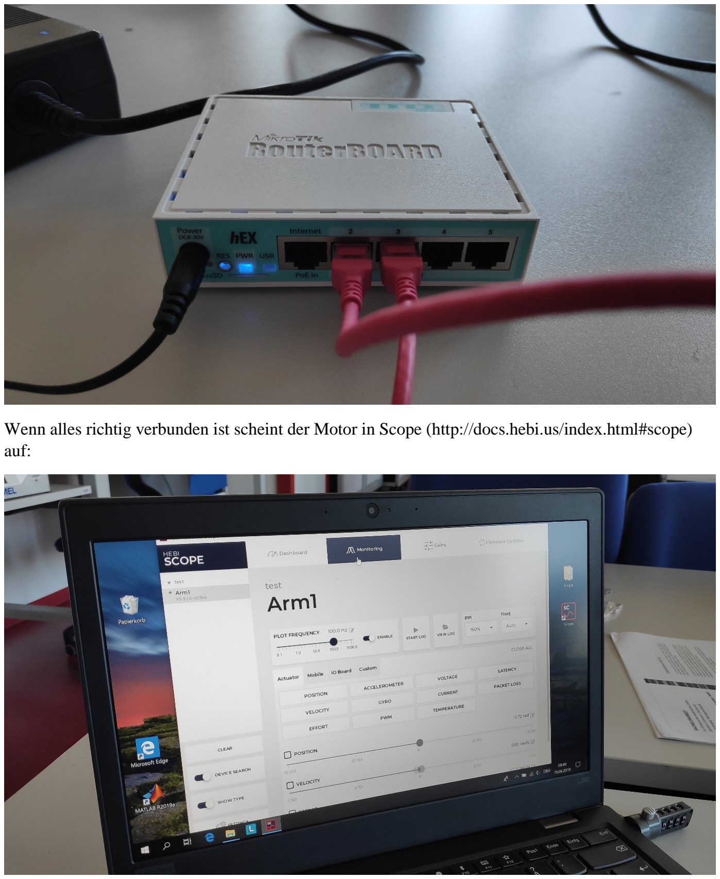
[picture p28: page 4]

Wenn alles richtig verbunden ist scheint der Motor in Scope (http://docs.hebi.us/index.html#scope) auf:

Der finale Aufbau:

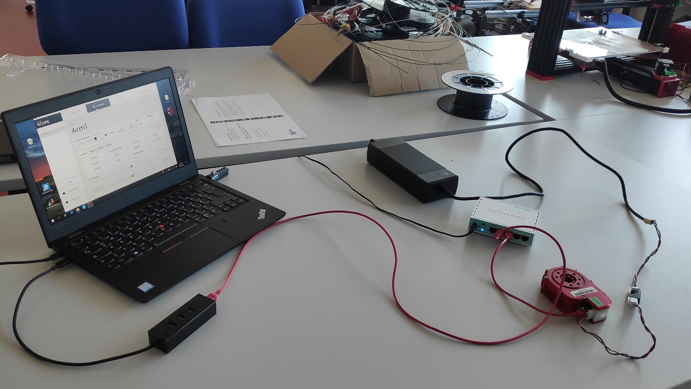
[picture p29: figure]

Anschließend die MATLAB Ordnerstruktur öffnen:

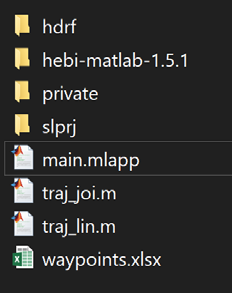
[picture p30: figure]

Das Matlab Skript “main.mlapp” ausführen, dies ist das GUI um den Roboter zu bedienen. Alternativ können auch die Skripte “traj_joi” zum achsweisen Verfahren oder “trai_lin” zum linearen Verfahren des Roboters gestartet werden.
In der Excel Tabelle “waypoints.xlsx” sind die Wegpunkte des Roboters hinterlegt.

Im geöffneten GUI die Punkte “plot trajectory info” und “plot trajectory profile” anhaken um alle Informationen einsehen zu können. Danach die Methode zum Verfahren des linearen Pfades wählen (empfohlen: cubic spline data interpolation) und zum Starten des Roboters auf “MoveL” klicken.
